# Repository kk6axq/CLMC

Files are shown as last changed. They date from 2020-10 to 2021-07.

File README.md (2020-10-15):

# CLMC (Closed Loop Motor Controller)
This is a closed loop brushed DC motor controller project, completed for an honors enrichment contract in EGR101 at Arizona State University. The goal was to develop the hardware and software to enabled PID based control of position, velocity, and acceleration in an encoder equipped motor. So far, the project has met its minimum requirements, however there are several areas to improve. For more background on the project and architectures, see the Wiki.

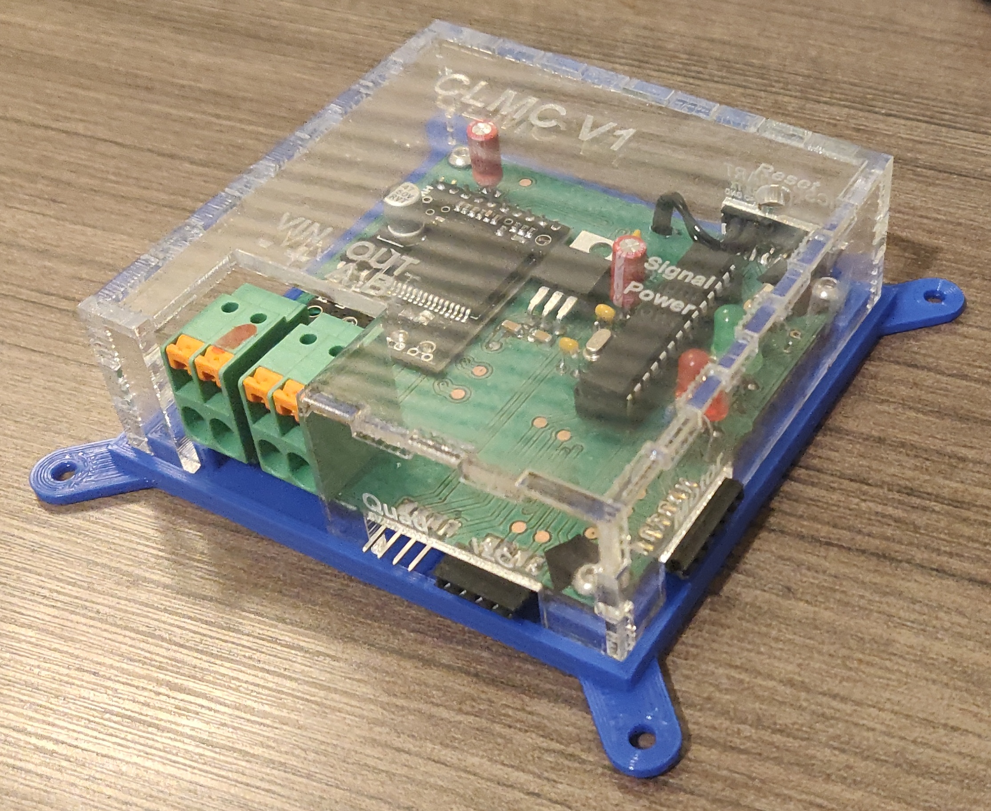
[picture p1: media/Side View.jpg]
Board Photo


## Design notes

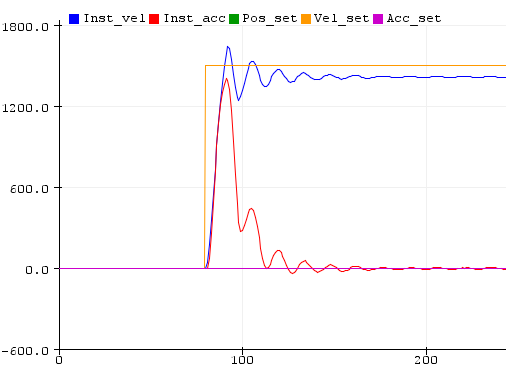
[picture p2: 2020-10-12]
media/Constant Vel Graph - Without Pos.PNG

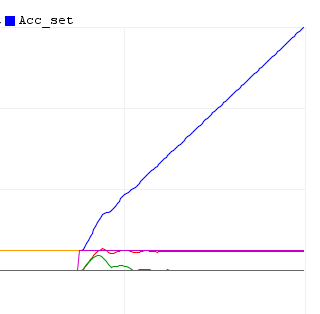
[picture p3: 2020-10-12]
media/Constant Vel Graph - With Pos.PNG

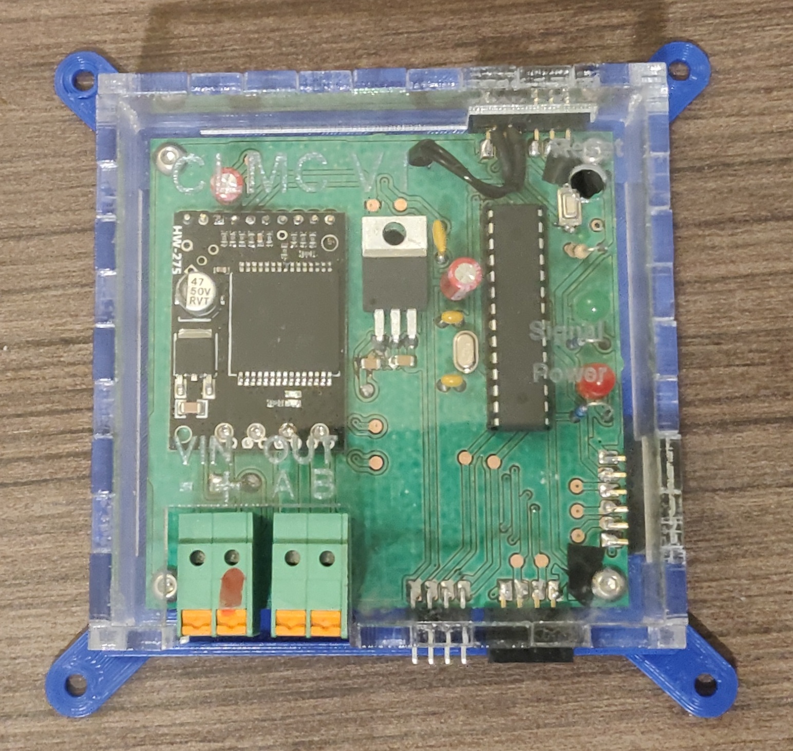
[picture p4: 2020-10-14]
media/Top View.jpg

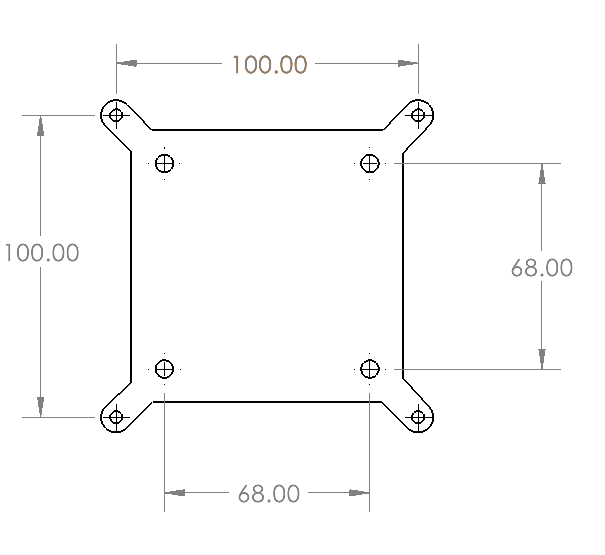
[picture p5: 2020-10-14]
media/Hole Pattern.PNG

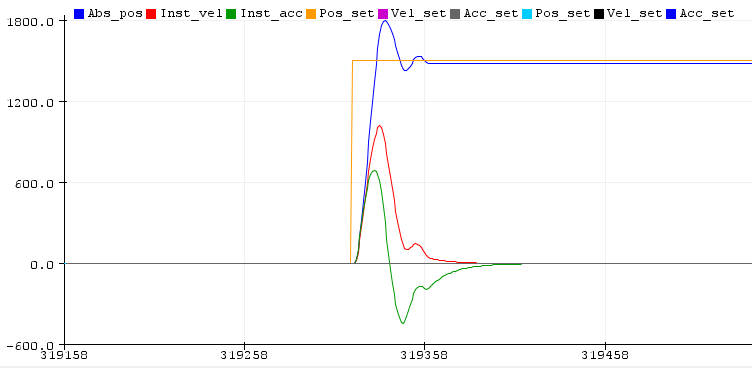
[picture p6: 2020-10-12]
media/Constant Pos Graph.PNG

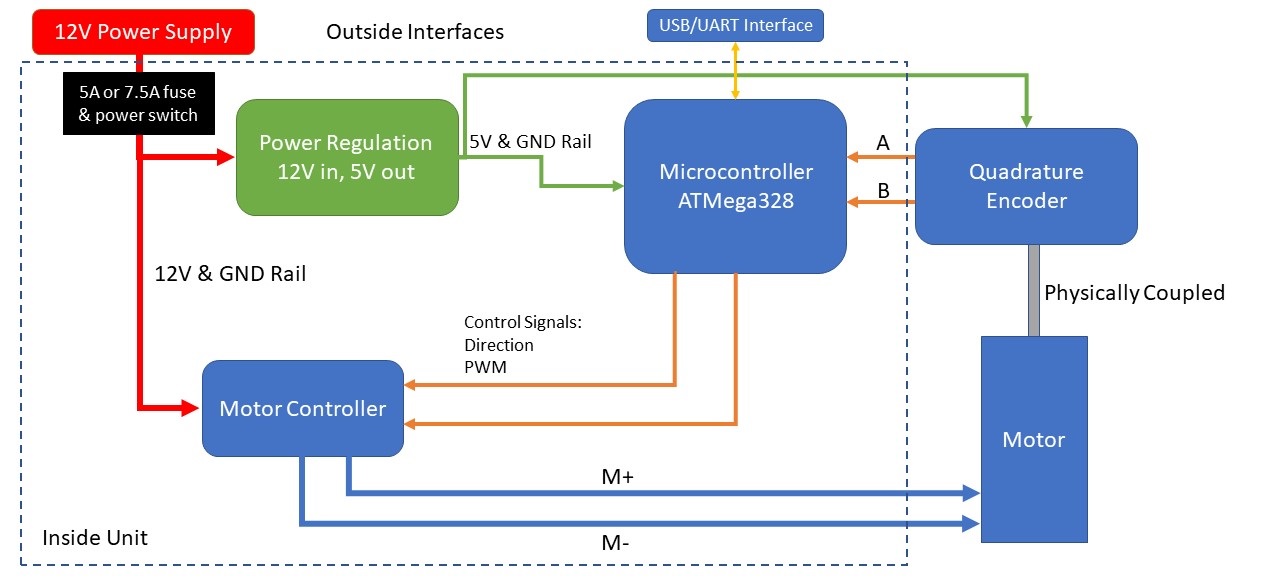
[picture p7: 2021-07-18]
media/Block Diagram.jpg

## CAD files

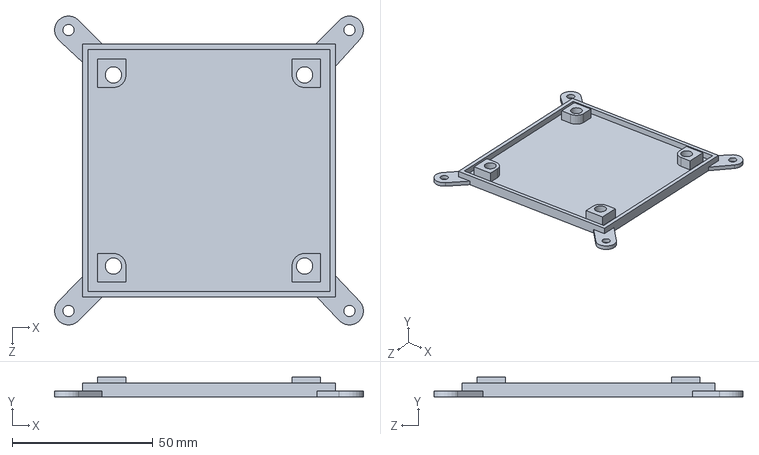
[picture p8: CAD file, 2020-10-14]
hardware/CAD/Main Board Enclosure/PCB Enclosure V1.SLDPRT
109.9 x 7.00 x 109.9 mm

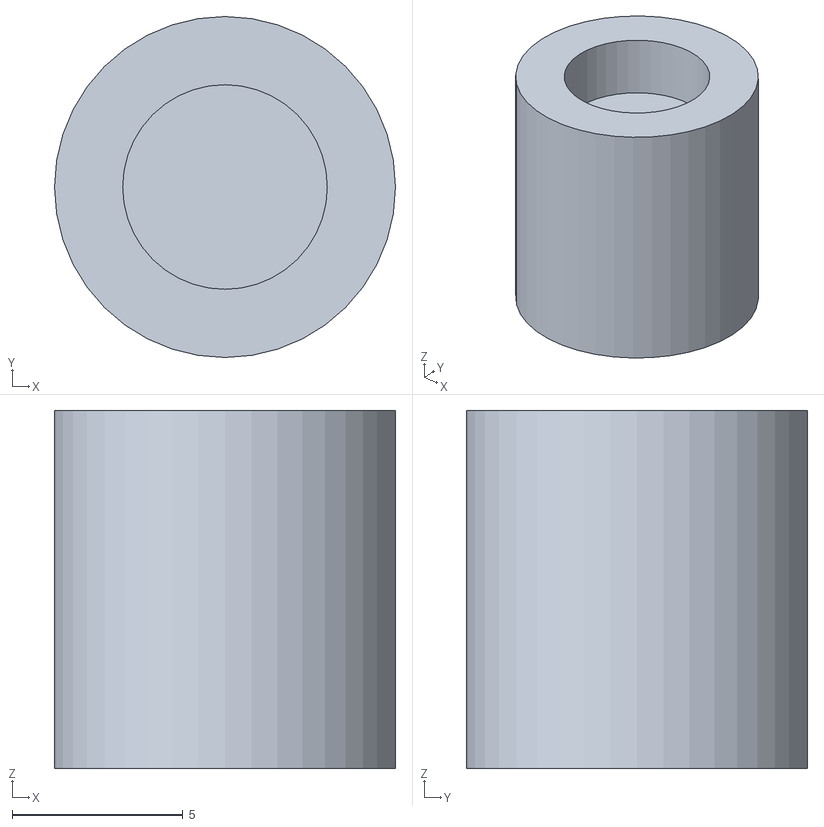
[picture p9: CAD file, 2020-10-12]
hardware/CAD/Motor Magnet Mount/Motor Magnet Mount.stl
10.0 x 10.0 x 10.5

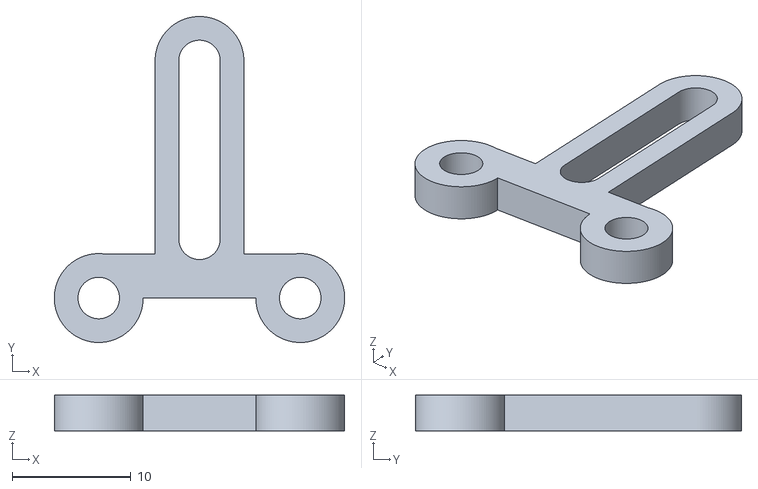
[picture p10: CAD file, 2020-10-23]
hardware/CAD/Sensor Motor Mount/Upper Piece V1.stl
24.5 x 27.5 x 3.00

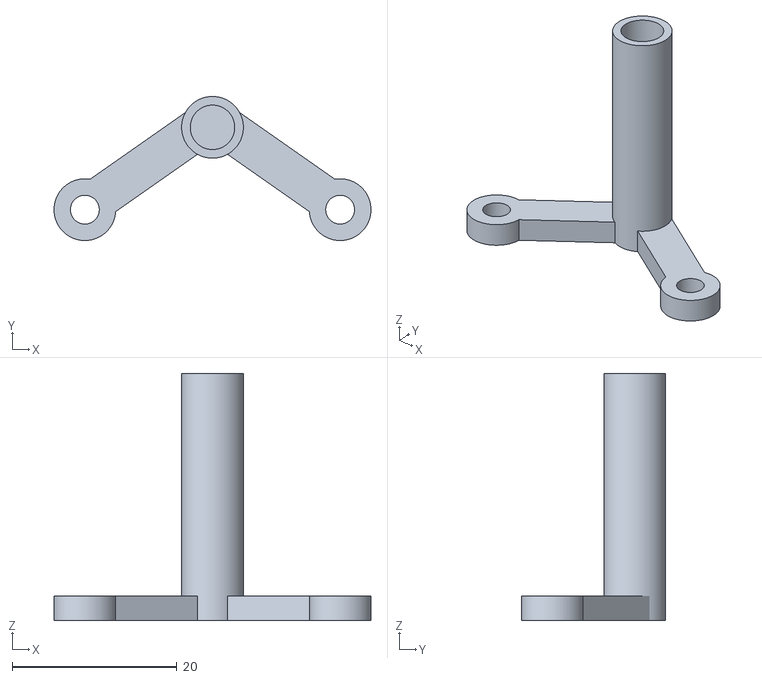
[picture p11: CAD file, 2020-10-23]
hardware/CAD/Sensor Motor Mount/Base Piece V2.stl
38.5 x 17.5 x 30.0

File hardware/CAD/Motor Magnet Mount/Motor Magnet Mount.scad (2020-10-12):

/*
Parametric Magnet Holder
Lukas Severinghaus
September 12, 2020
This program generates a 3d model to hold a magnet of a certain size
on top of a keyed axle. All the dimensions can be changed in the 
variables below.
This program is measurement unit independent.
*/

//Height of the motor axle
axle_height = 6;
//Radius of the motor axle
axle_radius = 3.35; //3.1 was too small
//Distance from the center of the axle to where the key starts
key_offset = 2.4;


//Height of the layer between the motor axle and magnet
separator_height = 2;

//Magnet dimensions
magnet_height = 2.5;
magnet_radius = 3.5; //3.2 was too small

//Wall thickness of the piece
wall_thickness = 2;

//Advanced config parameters
//How many lines to break the circle into
circle_resolution = 80;

//How much extra to cut through the faces, smaller is better
cut_offset = 0.1;

//Radius of the outer containing cylinder.
outer_radius = max(magnet_radius, axle_radius) + wall_thickness;

total_height = axle_height + separator_height + magnet_height;
//Cut the magnet hole
difference(){
    //Cut the axle keyed hole out of the bottom of the piece
    difference() {
        //Define the base cylinder
        cylinder(total_height, outer_radius, outer_radius, $fn=circle_resolution);
        //Move the cylinder down a little to fully cut through the face
        translate([0, 0, -1 * cut_offset]){
            //Cut the key in the shaft
            difference() {
                //Define the shaft cylinder
                cylinder(axle_height + cut_offset, axle_radius, axle_radius, $fn=40);
                //Translate and define the key rectangle
                translate([key_offset, -1 * axle_radius, 0]) {
                    cube([axle_radius - key_offset + cut_offset, axle_radius * 2, axle_height + cut_offset]);
                }
            }
        }
    }

    translate([0, 0, axle_height + separator_height]) {
        cylinder(magnet_height + cut_offset, magnet_radius, magnet_radius, $fn=circle_resolution);
    }
    
    translate([4.5, -10, -1 * cut_offset]) cube([1,25, 20]);
}

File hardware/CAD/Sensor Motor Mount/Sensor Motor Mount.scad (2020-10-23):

/*
Two Piece Motor Mount
Lukas Severinghaus
October 22, 2020
Generates a motor mount to hold the sensor PCB. 
Sized to fit a Pololu 37mm diameter gear motor.
*/

//Set to 1 to view entire assembly
//Set to 2 to view only the base
//Set to 3 to view only the top
view = 1;


hole_size=3.5;
base_hole_spacing = 31;
cr = 100;

post_s = 2;
post_h = 30;

base_h = 3;

top_spacing = 17;

module base(){
difference(){
    union(){
        //Tower
        translate([0, 10, 0]) cylinder(post_h, r1=hole_size/2+2, r2=hole_size/2+2, $fn=cr);
        //Holes

        //Base pieces
        translate([0, 8, 0]) rotate([0, 0, -35]) cube([15, base_h+2, base_h]);
        translate([0, 8, 0]) rotate([0, 0, 180+35]) translate([0, -base_h-2, 0]) cube([15, base_h+2, base_h]);
        translate([-1 * (base_hole_spacing / 2), 0, 0]) cylinder(base_h, r1=hole_size/2+2, r2=hole_size/2+2, $fn=cr);

        translate([(base_hole_spacing / 2), 0, 0]) cylinder(base_h, r1=hole_size/2+2, r2=hole_size/2+2, $fn=cr);
            }

        translate([-1 * (base_hole_spacing / 2), 0, -0.1]) cylinder(5, r1=hole_size/2, r2=hole_size/2, $fn=cr);

        translate([(base_hole_spacing / 2), 0, -0.1]) cylinder(5, r1=hole_size/2, r2=hole_size/2, $fn=cr);
        translate([0, 10, base_h]) cylinder(30, r1=2.7, r2=2.7, $fn=cr);
    }
}
//base();
module upper(){
    difference(){
    union(){
    translate([top_spacing / 2 * -1, 0, 0]) cylinder(base_h, r1=hole_size/2+2, r2=hole_size/2+2, $fn=cr);
    translate([top_spacing / 2, 0, 0]) cylinder(base_h, r1=hole_size/2+2, r2=hole_size/2+2, $fn=cr);
    translate([-9, 0, 0]) cube([18, 3.7, base_h]);
    translate([-1 * (hole_size/2+2), 0, 0]) cube([hole_size+4, 20, base_h]);
    translate([0, 20, 0]) cylinder(base_h, r1=hole_size/2+2, r2=hole_size/2+2, $fn=cr);
    }
    translate([top_spacing / 2 * -1, 0, -0.1]) cylinder(base_h+2, r1=hole_size/2, r2=hole_size/2, $fn=cr);
    translate([top_spacing / 2, 0, -0.1]) cylinder(base_h+2, r1=hole_size/2, r2=hole_size/2, $fn=cr);
    translate([0, 20, -0.1]) cylinder(base_h+0.2, r1=hole_size/2, r2=hole_size/2, $fn=cr);
    translate([0, 5, -0.1]) cylinder(base_h+0.2, r1=hole_size/2, r2=hole_size/2, $fn=cr);
    translate([-1 * (hole_size / 2), 5, -0.1]) cube([hole_size, 15, base_h + 0.2]);
}
}
if(view==1){
    base();
    translate([0, -10, 30]) upper();
}else if(view == 2){
    base();
}else if(view == 3){
    upper();
}    

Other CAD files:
hardware/CAD/Main Board Enclosure/PCB Enclosure V1.STL

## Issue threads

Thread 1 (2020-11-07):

Current spikes on motor cold start

kk6axq, 2020-11-07:
When driving a Tetrix motor, there's an initial current spike when transitioning from a low output to full output (255 or -255), causing the microcontroller to reset when running on bench power.

Information:
The current sensor read a maximum of 2.06, however my bench power supply briefly triggered an over current warning at 6 amps. The signal LED flashed the startup sequence immediately after this and the previous command was not retained, so the microcontroller definitely reset.

Steps to reproduce:
* Connect to bench supply.
* Send the command `r1500`.
* Microcontroller resets.
Issue:
This probably stems from a brownout in the 5V rail, stemming from either the current protection reducing the voltage or the high current draw reducing the voltage. This suggests that there is a very brief high current spike when starting the motor to full speed.

The motor's internal resistance is 5-6 Ohms, which should draw 2A given V=IR, so that further supports the startup spike theory.

Possible solutions:
* Run it on battery power or a higher current supply. When powering it from a NiMH battery, the microcontroller does not reset.
* Add a capacitor to the 12V rail. This would maybe help keep the rail within the 5V regulator's usable range, though it might have to be a big capacitor.
* Add a capacitor to the 5V rail. This would buffer the 5V rail while the voltage drops, though I don't know what effect this would have on the motor driver.

kk6axq, 2020-11-18:
This is just inherent to the design. An additional capacitor could be added, but that distracts from the larger issue of not having a suitable power source. I'll close this for now and it can be reopened if it becomes an issue down the road.

Closed 2020-11-18.

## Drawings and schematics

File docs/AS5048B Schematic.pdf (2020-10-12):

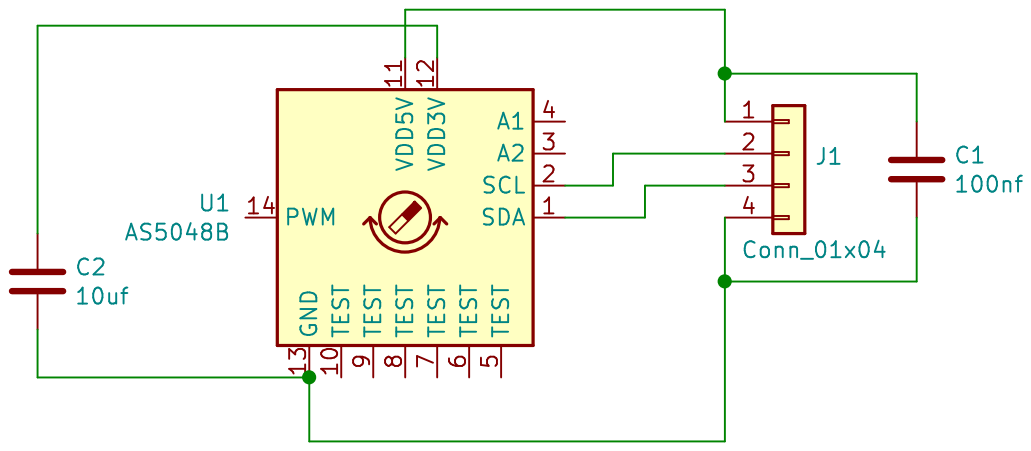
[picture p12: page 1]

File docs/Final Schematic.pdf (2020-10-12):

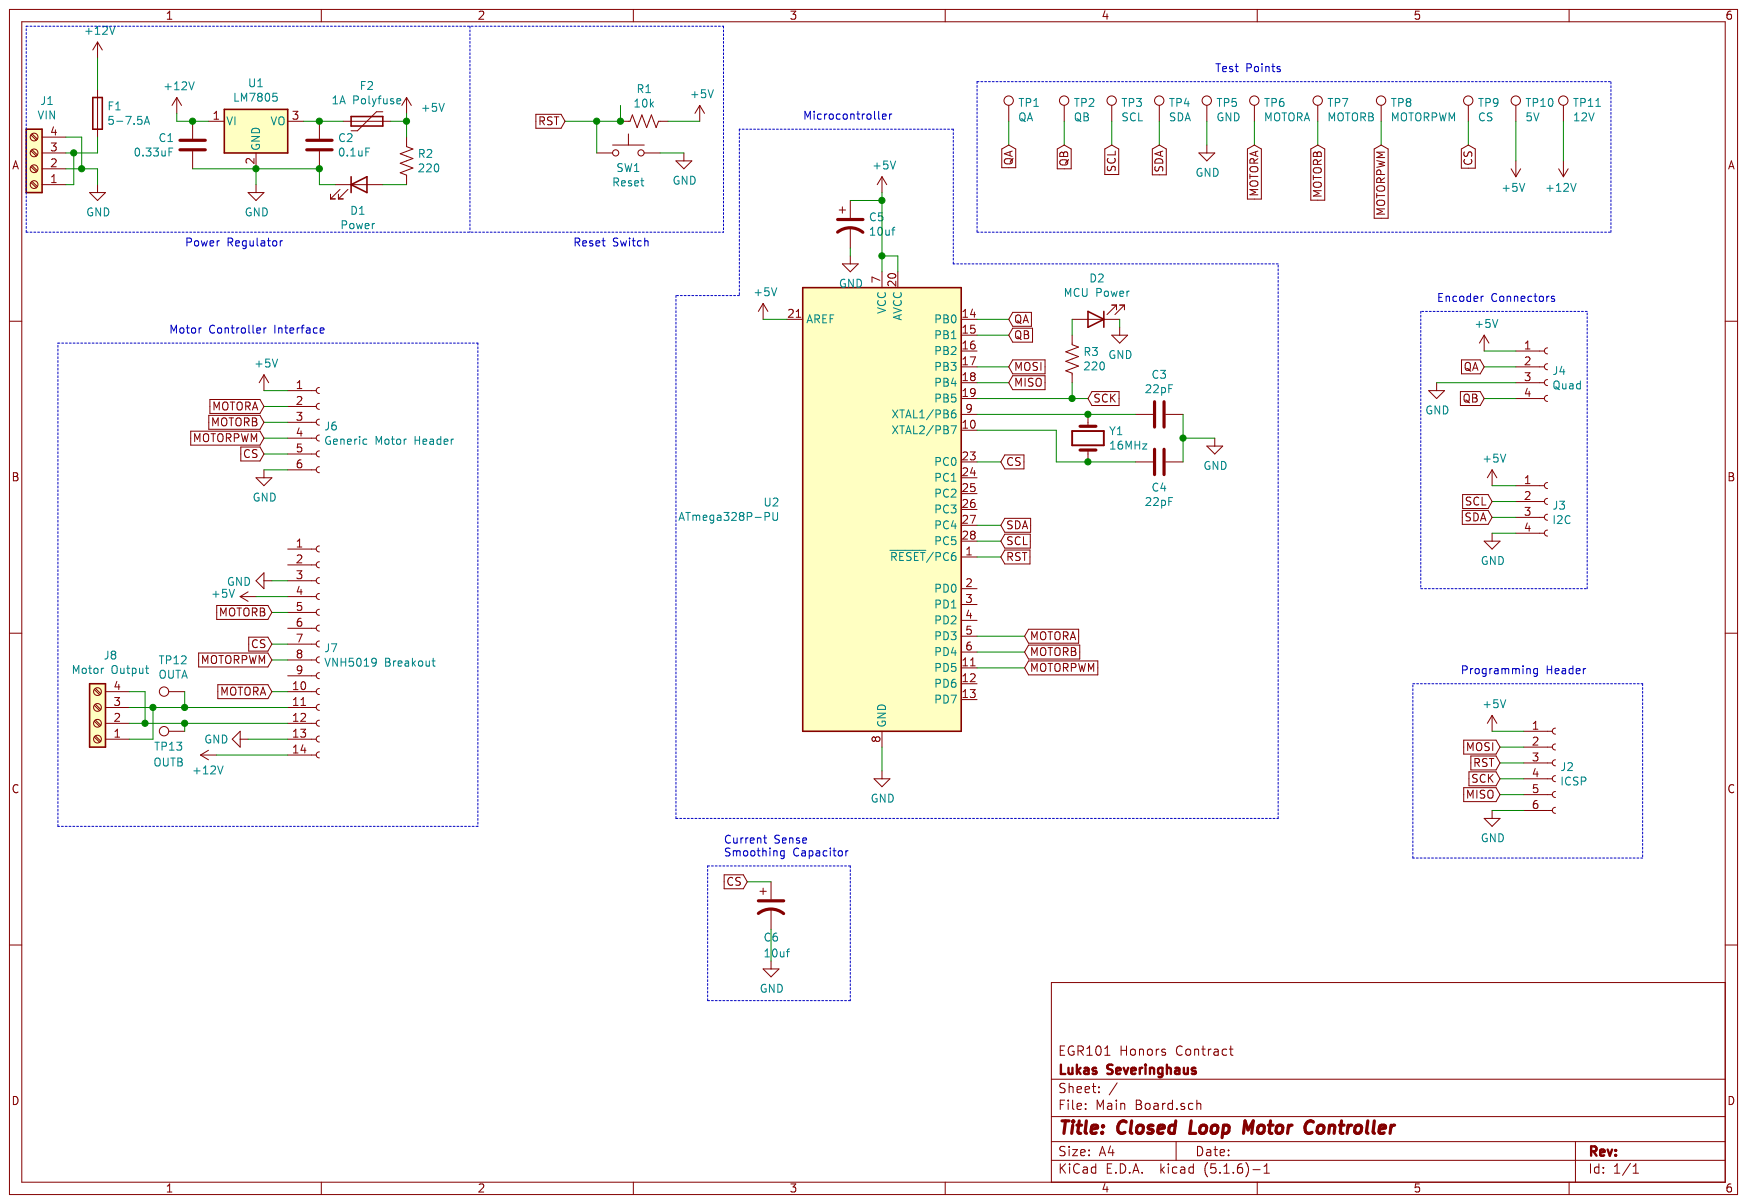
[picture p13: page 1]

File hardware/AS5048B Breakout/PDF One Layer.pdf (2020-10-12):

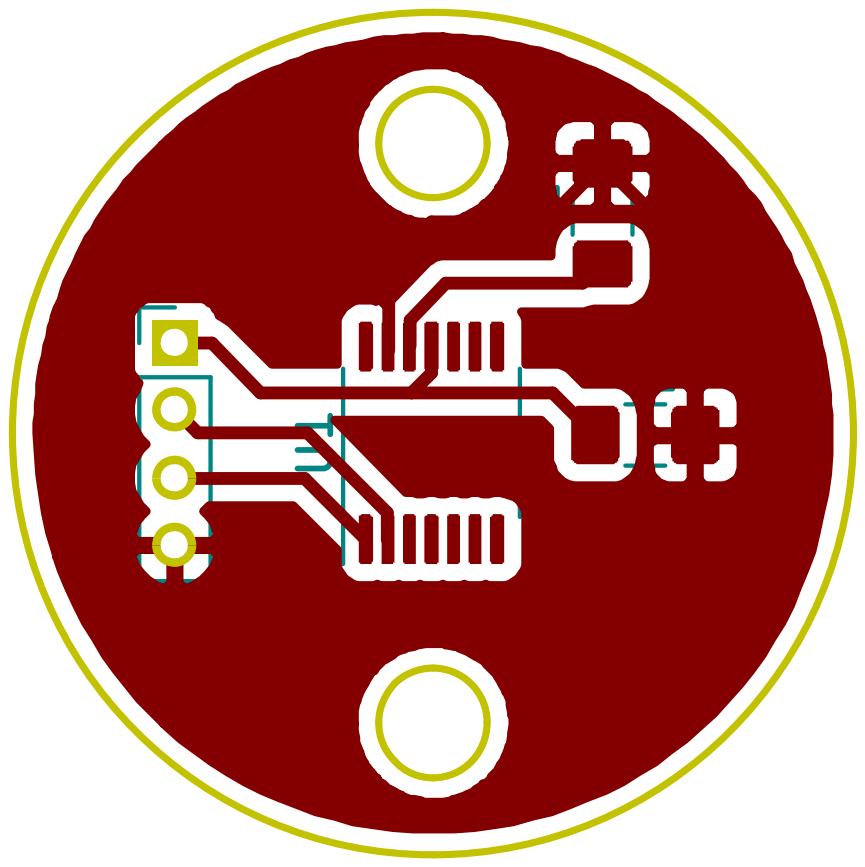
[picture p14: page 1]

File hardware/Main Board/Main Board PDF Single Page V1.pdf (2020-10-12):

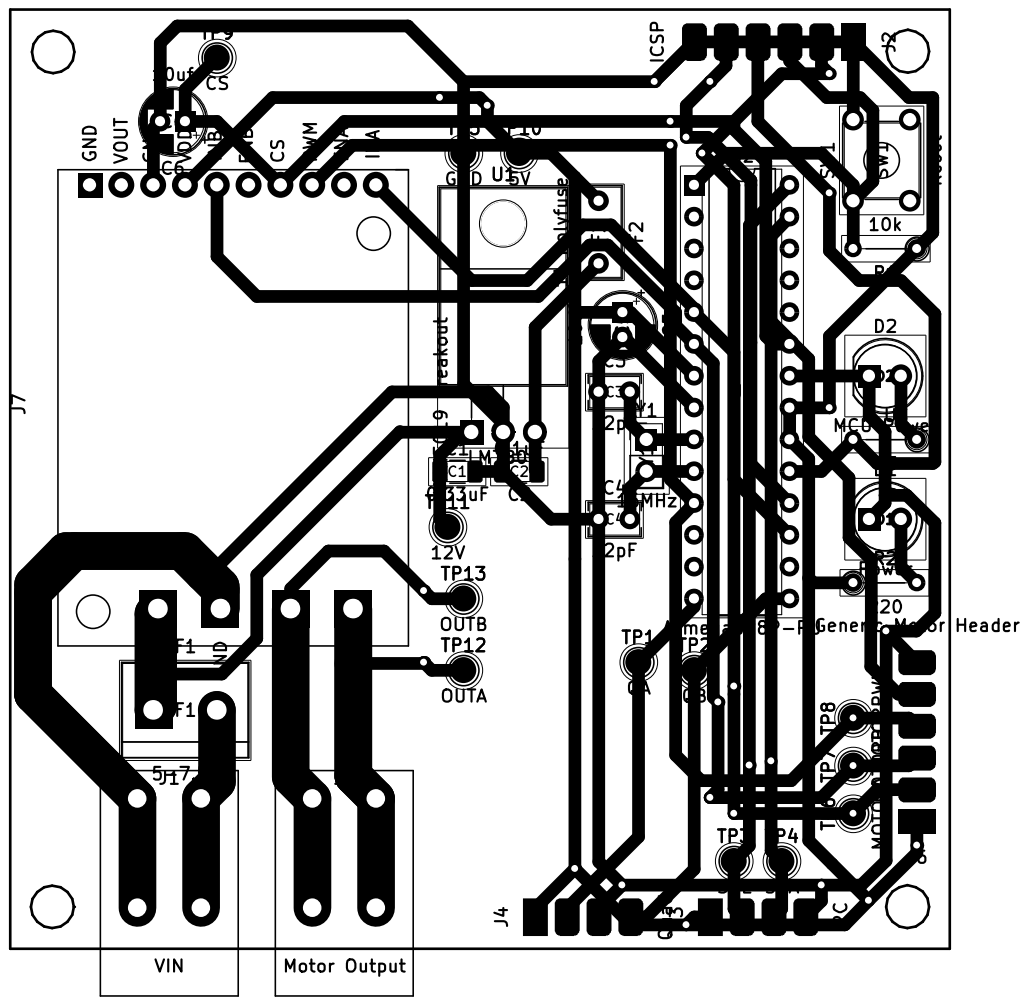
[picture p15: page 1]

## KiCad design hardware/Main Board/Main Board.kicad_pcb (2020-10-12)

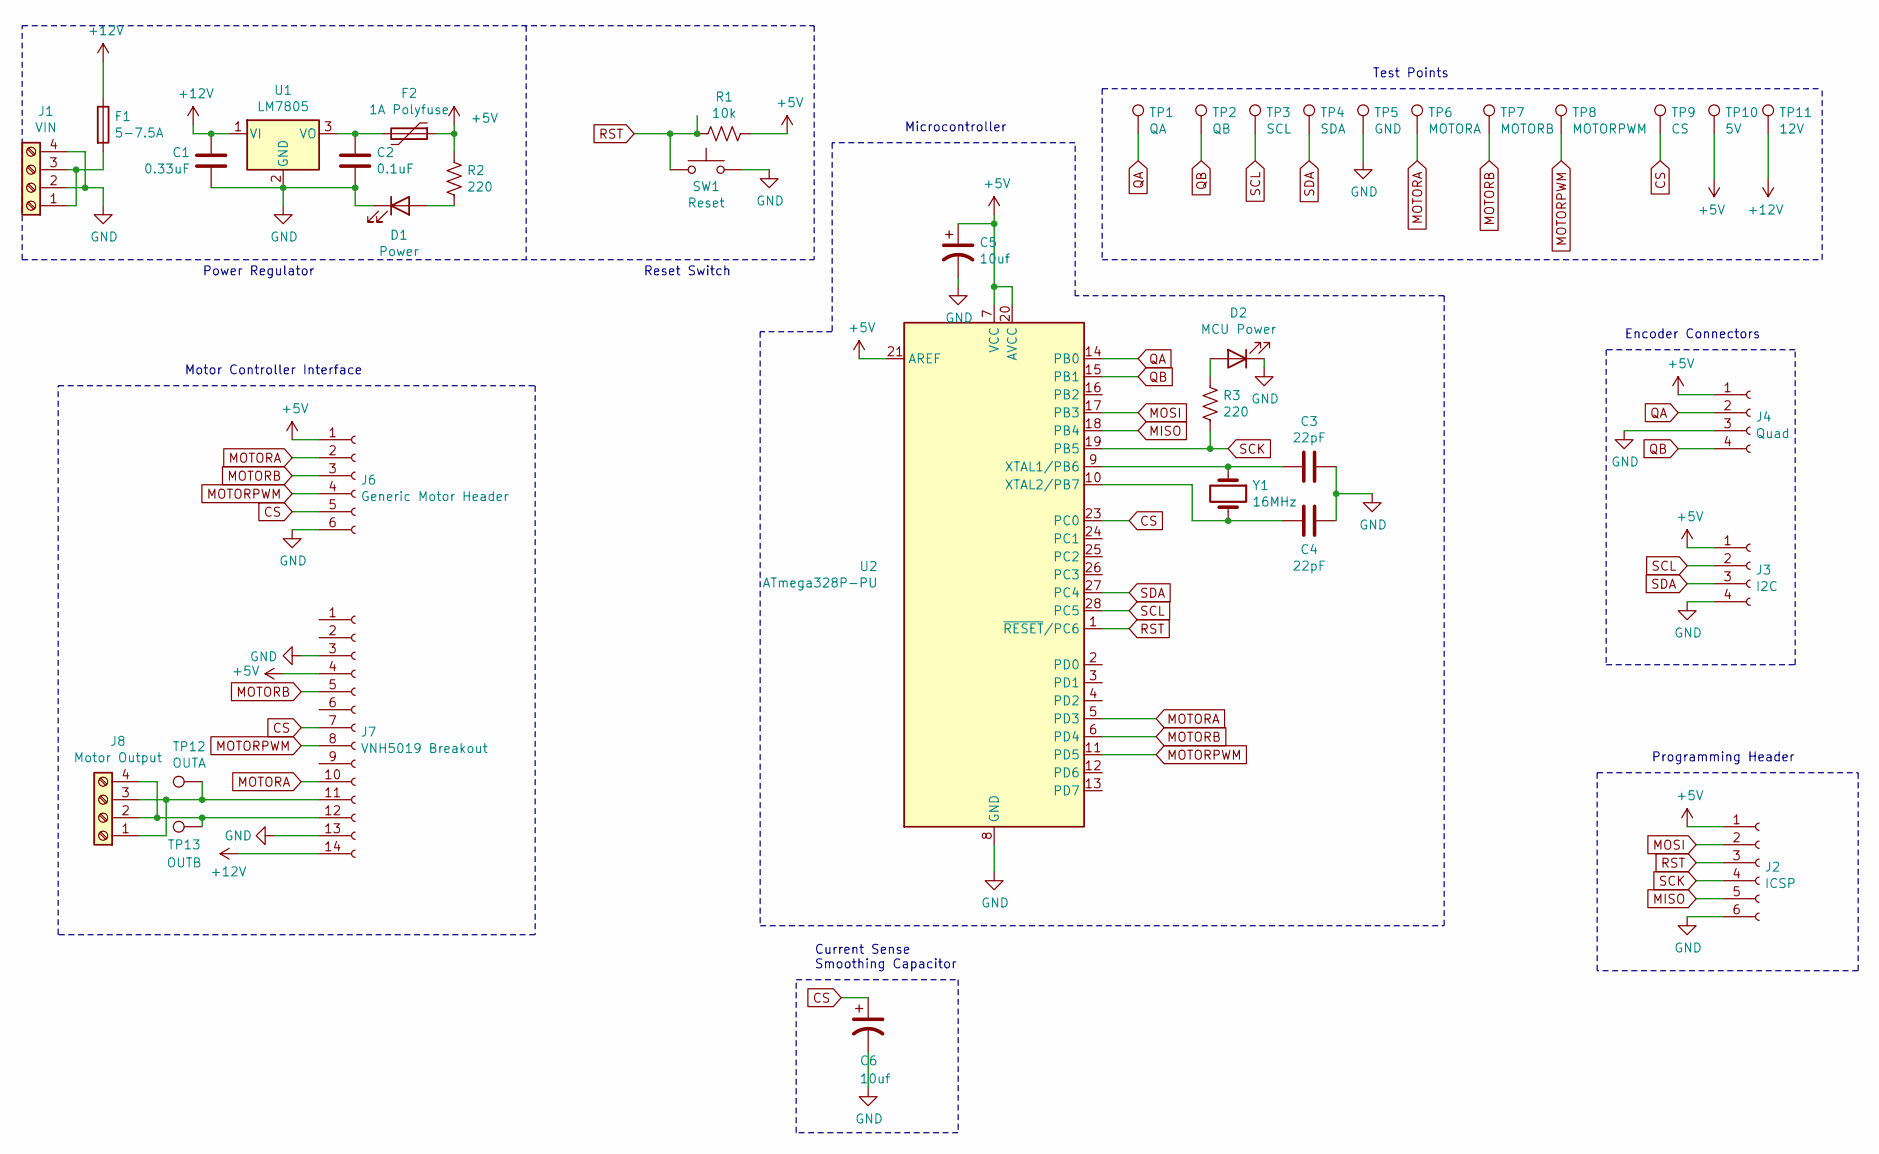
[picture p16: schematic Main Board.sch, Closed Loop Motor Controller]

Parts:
C1: 0.33uF; C_1206_3216Metric
C2: 0.1uF; C_1206_3216Metric
C3, C4: 22pF; C_Rect_L4.0mm_W2.5mm_P2.50mm
C5, C6: 10uf; CP_Radial_D5.0mm_P2.00mm
D1: Power; LED_D5.0mm
D2: MCU Power; LED_D5.0mm
F1: 5-7.5A; TerminalBlock_bornier-2_P5.08mm
F2: 1A Polyfuse; C_Rect_L7.2mm_W3.5mm_P5.00mm_FKS2_FKP2_MKS2_MKP2
J1: VIN; 2x2TerminalBlock
J2: ICSP; 6PinEdgeConnector
J3: I2C; 4PinEdgeConnector
J4: Quad; 4PinEdgeConnector
J6: Generic Motor Header; 6PinEdgeConnector
J7: VNH5019 Breakout; VNH5019Footprint
J8: Motor Output; 2x2TerminalBlock
R1: 10k; R_Axial_DIN0204_L3.6mm_D1.6mm_P5.08mm_Vertical
R2, R3: 220; R_Axial_DIN0204_L3.6mm_D1.6mm_P5.08mm_Vertical
SW1: Reset; SW_TH_Tactile_Omron_B3F-10xx
TP1: QA; TestPoint_Pad_D2.0mm
TP2: QB; TestPoint_Pad_D2.0mm
TP3: SCL; TestPoint_Pad_D2.0mm
TP4: SDA; TestPoint_Pad_D2.0mm
TP5: GND; TestPoint_Pad_D2.0mm
TP6: MOTORA; TestPoint_Pad_D2.0mm
TP7: MOTORB; TestPoint_Pad_D2.0mm
TP8: MOTORPWM; TestPoint_Pad_D2.0mm
TP9: CS; TestPoint_Pad_D2.0mm
TP10: 5V; TestPoint_Pad_D2.0mm
TP11: 12V; TestPoint_Pad_D2.0mm
TP12: OUTA; TestPoint_Pad_D2.0mm
TP13: OUTB; TestPoint_Pad_D2.0mm
U1: LM7805; TO-220-3_Horizontal_TabDown
U2: ATmega328P-PU; DIP-28_W7.62mm
Y1: 16MHz; PinHeader_1x02_P2.54mm_Vertical

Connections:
+5V: C5.1, F2.1, J2.1, J3.1, J4.1, J6.1, J7.4, R1.1, R2.1, TP10.1, U2.7 (VCC), U2.20 (AVCC), U2.21 (AREF)
+12V: C1.1, F1.1, J7.14, TP11.1, U1.1 (VI)
CS: C6.1, J6.5, J7.7, TP9.1, U2.23 (PC0)
GND: C1.2, C2.2, C3.1, C4.1, C5.2, C6.2, D1.1 (K), D2.1 (K), J1.2, J1.4, J2.6, J3.4, J4.3, J6.6, J7.3, J7.13, SW1.2, TP5.1, U1.2 (GND), U2.8 (GND), U2.22 (GND)
MISO: J2.5, U2.18 (PB4)
MOSI: J2.2, U2.17 (PB3)
MOTORA: J6.2, J7.10, TP6.1, U2.5 (PD3)
MOTORB: J6.3, J7.5, TP7.1, U2.6 (PD4)
MOTORPWM: J6.4, J7.8, TP8.1, U2.11 (PD5)
unnamed: C2.1, F2.2, U1.3 (VO)
unnamed: C3.2, U2.9 (XTAL1/PB6), Y1.1
unnamed: C4.2, U2.10 (XTAL2/PB7), Y1.2
unnamed: D1.2 (A), R2.2
unnamed: D2.2 (A), R3.1
unnamed: F1.2, J1.1, J1.3
unnamed: J7.11, J8.1, J8.3, TP12.1
unnamed: J7.12, J8.2, J8.4, TP13.1
QA: J4.2, TP1.1, U2.14 (PB0)
QB: J4.4, TP2.1, U2.15 (PB1)
RST: J2.3, R1.2, SW1.1, U2.1 (~RESET~/PC6)
SCK: J2.4, R3.2, U2.19 (PB5)
SCL: J3.2, TP3.1, U2.28 (PC5)
SDA: J3.3, TP4.1, U2.27 (PC4)

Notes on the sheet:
Power Regulator
Test Points
Programming Header
Encoder Connectors
Microcontroller
Reset Switch
Current Sense Smoothing Capacitor
Motor Controller Interface

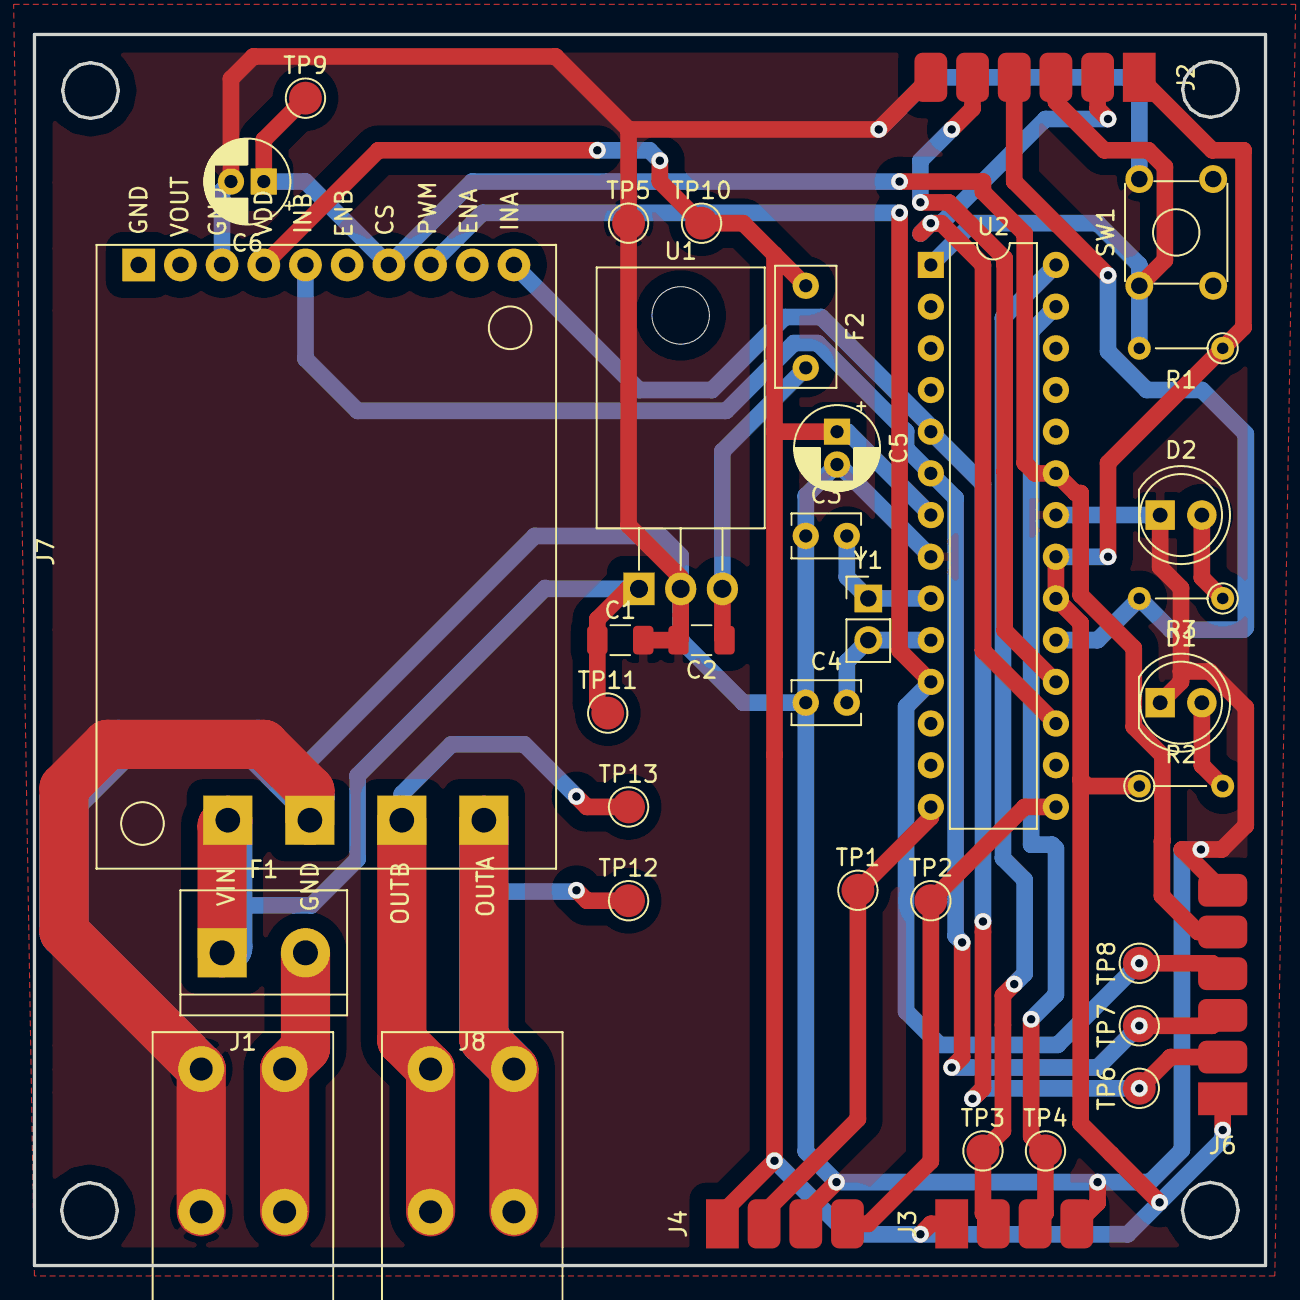
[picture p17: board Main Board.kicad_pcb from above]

Board: 2 copper layers, 75.0 x 75.0 mm, 37 parts (0 on the bottom side), 23 nets.

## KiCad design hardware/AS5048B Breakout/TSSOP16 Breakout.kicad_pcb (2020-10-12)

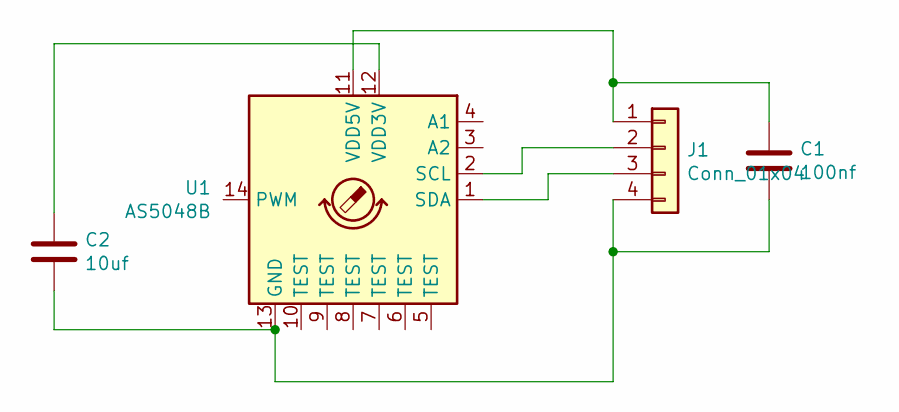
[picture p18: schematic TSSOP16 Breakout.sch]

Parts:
C1: 100nf; C_1206_3216Metric_Pad1.42x1.75mm_HandSolder
C2: 10uf; C_1206_3216Metric_Pad1.42x1.75mm_HandSolder
J1: Conn_01x04; PinHeader_1x04_P2.00mm_Vertical
U1: AS5048B; TSSOP-14_4.4x5mm_P0.65mm

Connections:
unnamed: C1.1, J1.1, U1.11 (VDD5V)
unnamed: C1.2, C2.2, J1.4, U1.13 (GND)
unnamed: C2.1, U1.12 (VDD3V)
unnamed: J1.2, U1.2 (SCL)
unnamed: J1.3, U1.1 (SDA)

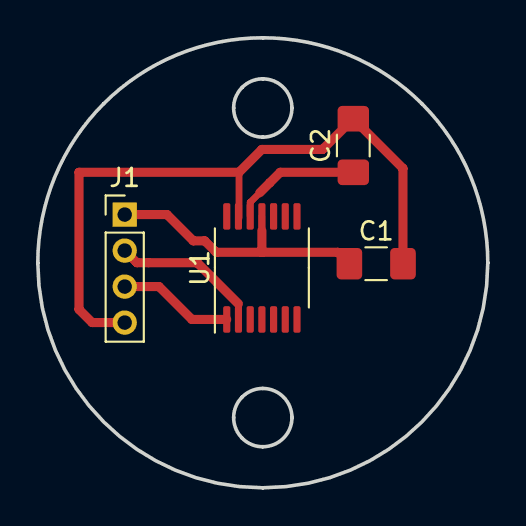
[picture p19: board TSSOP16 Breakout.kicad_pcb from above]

Board: 2 copper layers, 25.0 x 25.0 mm, 4 parts (0 on the bottom side), 5 nets.

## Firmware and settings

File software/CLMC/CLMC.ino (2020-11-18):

/**
   File: CLMC.ino
   Author: Lukas Severinghaus
   Date: October 11, 2020
   Purpose: Control code for ATMega328p based PID motor controller.
   Completed as part of an honors enrichment contract for EGR101 at ASU.

   License:
   Copyright (C) 2020  Lukas Severinghaus

   This program is free software; you can redistribute it and/or
   modify it under the terms of the GNU General Public License version 3
   as published by the Free Software Foundation;

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
   You should have received a copy of the GNU General Public License
   along with this program; if not, write to the Free Software
   Foundation, Inc., 51 Franklin Street, Fifth Floor, Boston, MA  02110-1301, USA.
*/
//Uncomment to load config and PIDs from EEPROM on boot.
#define LOAD_CONFIG_ON_BOOT

//Serial baud rate
#define BAUD_RATE 9600

//Pin that signalling LED is connected to
#define LED_PIN 13



#define TUNE_NONE 0
#define TUNE_POS 1
#define TUNE_VEL 2
#define TUNE_ACC 3
void setup() {

  Serial.begin(BAUD_RATE);

  init_motor();
  init_encoders();
  init_pid();

  pinMode(LED_PIN, OUTPUT);
  for (int i = 0; i < 3; i++) {
    digitalWrite(LED_PIN, HIGH);
    delay(100);
    digitalWrite(LED_PIN, LOW);
    delay(100);
  }
#ifdef LOAD_CONFIG_ON_BOOT
  load_config();
#endif
}

//Flag for enabling motor output.
bool control = true;

void loop() {
  //Read from Serial, if bytes are available
  if (Serial.available() > 0) {
    char s = Serial.read();
    //Check if the character matches a command letter
    if (s == 'r') {
      constant_pos(Serial.parseInt());
    } else if (s == 'f') {
      constant_vel(Serial.parseInt());
    } else if (s == 'v') {
      constant_acc(Serial.parseFloat());
    } else if (s == 'e') {
      control = true;
    } else if (s == 'w') {
      control = false;
      command_motor(0);
    } else if (s == 'p') {
      tune_p(Serial.parseFloat());
    } else if (s == 'i') {
      tune_i(Serial.parseFloat());
    } else if (s == 'd') {
      tune_d(Serial.parseFloat());
    } else if (s == 's') {
      if (get_tune_mode() == TUNE_POS || get_tune_mode() == TUNE_VEL) {
        command_tune(Serial.parseInt());
      } else if (get_tune_mode() == TUNE_ACC) {
        command_tune(Serial.parseFloat());
      } else {
        Serial.println("No tuning mode currently set.");
      }
    } else if (s == 't') { //Set controller to tune.
      serial_wait_timeout(1, 20);
      char a = Serial.read();
      Serial.println(a);
      if (a == 'p') {
        Serial.println("Selecting position controller");
        set_tune_mode(TUNE_POS);
      } else if (a == 'v') {
        Serial.println("Selecting velocity controller");
        set_tune_mode(TUNE_VEL);
      } else if (a == 'a') {
        Serial.println("Selecting acceleration controller");
        set_tune_mode(TUNE_ACC);
      } else {
        Serial.println("Deselecting tuned controller");
        set_tune_mode(TUNE_NONE);
      }
    } else if (s == 'j') {
      set_inst_vel_filter(Serial.parseFloat());
    } else if (s == 'l') {
      Serial.println("Loading config from EEPROM");
      load_config();
    } else if (s == 'k') {
      Serial.println("Saving config to EEPROM");
      save_config();
    } else if (s == 'z') {
      print_pids();
    } else if (s == 'x') {
      print_EEPROM();
    } else if (s == 'h') {
      Serial.println("\n**** Commands ****");
      Serial.println("r<int>\tConstant Position");
      Serial.println("f<int>\tConstant Velocity");
      Serial.println("v<float>\tConstant Acceleration");
      Serial.println("e\tEnable Output");
      Serial.println("w<int>\tDisable Output");
      Serial.println("t[p,v,a]\tSelect controller to tune");
      Serial.println("p<float>\tSet P component of tuned controller");
      Serial.println("i<float>\tSet I component of tuned controller");
      Serial.println("d<float>\tSet D component of tuned controller");
      Serial.println("j<float>\tSet strength of velocity particle filter");
      Serial.println("z\tPrint PID values");
      Serial.println("x\tPrint EEPROM values");
      Serial.println("k\tSave configuration to EEPROM");
      Serial.println("l\tLoad configuration from EEPROM");
      Serial.println("h\tShow help menu");
    }
  }


  //Diagnostic output:
  //Measured outputs, position, velocity, and acceleration
  Serial.print("Inst_vel: ");
  Serial.print(get_inst_velocity());
  Serial.print("\tInst_acc: ");
  Serial.print(get_inst_acceleration());

  if (get_tune_mode() == TUNE_POS) {
    Serial.print("\tAbs_pos: ");
    Serial.print(get_raw_count());
  }
  //Setpoints
  Serial.print("\tPos_set: ");
  Serial.print(get_pos_setpoint());
  Serial.print("\tVel_set: ");
  Serial.print(get_vel_setpoint());
  Serial.print("\tAcc_set: ");
  Serial.print(get_acc_setpoint());
  Serial.print("\tOutput: ");
  Serial.print(get_pid_output());
  Serial.print("\tCurrent: ");
  Serial.print(get_current());
  Serial.println();

  update_pid();
  if (control) command_motor(get_pid_output());

}
/**
 * Waits for serial bytes, or timeout, whichever comes first.
 * len: number of bytes to wait for.
 * timeout: timeout in ms to wait for bytes.
 * Returns nothing.
 */
void serial_wait_timeout(int len, int timeout){
  long start_t = millis();
  while(Serial.available() < len && millis() < timeout + start_t);
  Serial.print("Waited: "); Serial.println(millis() - start_t);
}
bool get_control() {
  return control;
}

void set_control(bool val) {
  control = val;
}

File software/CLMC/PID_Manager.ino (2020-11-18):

/**
   File: PID_Manager.ino
   Author: Lukas Severinghaus
   Date: October 11, 2020
   Purpose: Interfaces with PID control library.

   License:
   Copyright (C) 2020  Lukas Severinghaus

   This program is free software; you can redistribute it and/or
   modify it under the terms of the GNU General Public License version 3
   as published by the Free Software Foundation;

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
   You should have received a copy of the GNU General Public License
   along with this program; if not, write to the Free Software
   Foundation, Inc., 51 Franklin Street, Fifth Floor, Boston, MA  02110-1301, USA.
*/
/**
   Sources referenced during development:
   Filter: https://dsp.stackexchange.com/questions/41854/low-pass-filter-algorithm-origin
*/

#define TUNE_ERROR "Not currently in tuning mode."
byte tune_mode = TUNE_NONE;

//Constant velocity error is change in position for right now + error from last period
#define CONSTANT_ACC 0
#define CONSTANT_VEL 1
#define CONSTANT_POS 2
#define RAW 3

#include <PIDController.h>

PIDController position_controller;
PIDController velocity_controller;
PIDController acceleration_controller;
int pid_freq = 50;
int pid_period = 1000 / pid_freq;
long last_pid_loop = 0;


float pos_kp = 2;
float pos_ki = 0.2;
float pos_kd = 0;


float vel_kp = 1;
float vel_ki = 0.4;
float vel_kd = 0.3;

float acc_kp = 0.8;
float acc_ki = 0.3;
float acc_kd = 0;

double pos_setpoint = 0;
double vel_setpoint = 0;
double acc_setpoint = 0;

byte current_state = RAW;

void init_pid() {
  position_controller.begin();
  position_controller.setpoint(pos_setpoint);
  position_controller.tune(pos_kp, pos_ki, pos_kd);
  position_controller.limit(-255, 255);

  velocity_controller.begin();
  velocity_controller.setpoint(vel_setpoint);
  velocity_controller.tune(vel_kp, vel_ki, vel_kd);
  velocity_controller.limit(-255, 255);

  acceleration_controller.begin();
  acceleration_controller.setpoint(acc_setpoint);
  acceleration_controller.tune(acc_kp, acc_ki, acc_kd);
  acceleration_controller.limit(-255, 255);
}
void update_pid() {
  if (millis() > last_pid_loop + pid_period) {
    calculate_instantaneous();
    if (current_state == CONSTANT_ACC) {
      acceleration_controller.compute(get_inst_acceleration());
    } else if (current_state == CONSTANT_VEL) {
      velocity_controller.compute(get_inst_velocity());
    } else if (current_state == CONSTANT_POS) {
      position_controller.compute(get_raw_count());
    } else if (current_state == RAW) {
      //Do nothing.
    }
  }
}

int get_pid_output() {
  if (current_state == CONSTANT_ACC) {
    return acceleration_controller.getOutput();
  } else if (current_state == CONSTANT_VEL) {
    return velocity_controller.getOutput();
  } else if (current_state == CONSTANT_POS) {
    return position_controller.getOutput();
  } else {
    return 0; //Fail safe, if in raw mode.
  }
}
void set_state(int st) {
  current_state = st;
}
void constant_pos(long setpoint) {
  set_state(CONSTANT_POS);
  pos_setpoint = setpoint;
  position_controller.setpoint(setpoint);
}

void constant_vel(float vel) {
  set_state(CONSTANT_VEL);
  vel_setpoint = vel;
  velocity_controller.setpoint(vel);
}

void constant_acc(float acc) {
  set_state(CONSTANT_ACC);
  acc_setpoint = acc;
  acceleration_controller.setpoint(acc);
}

/**** Setpoint getters ****/
int get_pos_setpoint() {
  return pos_setpoint;
}

int get_vel_setpoint() {
  return vel_setpoint;
}

int get_acc_setpoint() {
  return acc_setpoint;
}
/**** Position PID modifiers ****/
void pos_p(float p) {
  pos_kp = p;
  update_pos_tune();
}

float pos_p() {
  return pos_kp;
}
void pos_i(float i) {
  pos_ki = i;
  update_pos_tune();
}

float pos_i() {
  return pos_ki;
}

void pos_d(float d) {
  pos_kd = d;
  update_pos_tune();
}

float pos_d() {
  return pos_kd;
}

void update_pos_tune() {
  position_controller.tune(pos_kp, pos_ki, pos_kd);
}
/**** Velocity PID modifiers ****/
void vel_p(float p) {
  vel_kp = p;
  update_vel_tune();
}

float vel_p() {
  return vel_kp;
}

void vel_i(float i) {
  vel_ki = i;
  update_vel_tune();
}

float vel_i() {
  return vel_ki;
}

void vel_d(float d) {
  vel_kd = d;
  update_vel_tune();
}

float vel_d() {
  return vel_kd;
}

void update_vel_tune() {
  velocity_controller.tune(vel_kp, vel_ki, vel_kd);
}
/**** Acceleration PID modifiers ****/
void acc_p(float p) {
  acc_kp = p;
  update_acc_tune();
}

float acc_p() {
  return acc_kp;
}

void acc_i(float i) {
  acc_ki = i;
  update_acc_tune();
}

float acc_i() {
  return acc_ki;
}

void acc_d(float d) {
  acc_kd = d;
  update_acc_tune();
}

float acc_d() {
  return acc_kd;
}

void update_acc_tune() {
  acceleration_controller.tune(acc_kp, acc_ki, acc_kd);
}

void tune_p(float p) {
  if (tune_mode == TUNE_POS) {
    pos_kp = p;
    update_pos_tune();
  } else if (tune_mode == TUNE_VEL) {
    vel_kp = p;
    update_vel_tune();
  } else if (tune_mode == TUNE_ACC) {
    acc_kp = p;
    update_acc_tune();
  }
}

void tune_i(float i) {
  if (tune_mode == TUNE_POS) {
    pos_ki = i;
    update_pos_tune();
  } else if (tune_mode == TUNE_VEL) {
    vel_ki = i;
    update_vel_tune();
  } else if (tune_mode == TUNE_ACC) {
    acc_ki = i;
    update_acc_tune();
  }
}

void tune_d(float d) {
  if (tune_mode == TUNE_POS) {
    pos_kd = d;
    update_pos_tune();
  } else if (tune_mode == TUNE_VEL) {
    vel_kd = d;
    update_vel_tune();
  } else if (tune_mode == TUNE_ACC) {
    acc_kd = d;
    update_acc_tune();
  } else {
    Serial.println(TUNE_ERROR);
  }
}
//Sets the setpoint of the currently active tune.
void command_tune(float val) {
  if (tune_mode == TUNE_POS) {
    constant_pos(val);
  } else if (tune_mode == TUNE_VEL) {
    constant_vel(val);
  } else if (tune_mode == TUNE_ACC) {
    constant_acc(val);
  } else {
    Serial.println(TUNE_ERROR);
  }

}

byte get_PID_current_state() {
  return current_state;
}

void set_PID_current_state(byte state) {
  current_state = state;
}

byte get_tune_mode() {
  return tune_mode;
}

void set_tune_mode(byte b) {
  tune_mode = b;
}

void print_pids(){
  Serial.println("**** PID Values ****");
  Serial.println("Position: ");
  Serial.print("\tP:"); Serial.println(pos_kp);
  Serial.print("\tI:"); Serial.println(pos_ki);  
  Serial.print("\tD:"); Serial.println(pos_kd);
  Serial.println("");
  Serial.println("Velocity: ");
  Serial.print("\tP:"); Serial.println(vel_kp);
  Serial.print("\tI:"); Serial.println(vel_ki);  
  Serial.print("\tD:"); Serial.println(vel_kd);
  Serial.println("");
  Serial.println("Acceleration: ");
  Serial.print("\tP:"); Serial.println(acc_kp);
  Serial.print("\tI:"); Serial.println(acc_ki);  
  Serial.print("\tD:"); Serial.println(acc_kd);
  Serial.println("**** End PID Values ****");  
}

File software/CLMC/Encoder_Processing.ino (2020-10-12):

/**
 * File: Encoder_Processing.ino
 * Author: Lukas Severinghaus
 * Date: October 11, 2020
 * Purpose: Handles processing of quadrature encoder data.
 * 
 * License:
 * Copyright (C) 2020  Lukas Severinghaus
 * 
 * This program is free software; you can redistribute it and/or
 * modify it under the terms of the GNU General Public License version 3
 * as published by the Free Software Foundation; 
 * 
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
 * You should have received a copy of the GNU General Public License
 * along with this program; if not, write to the Free Software
 * Foundation, Inc., 51 Franklin Street, Fifth Floor, Boston, MA  02110-1301, USA.
 */

/**
 * Encoder notes:
 * Channel A is connected to PCINT0, which is pin 8 on the Arduino Uno
 * Channel B is connected to PCINT1, which is pin 9 on the Arduino Uno
 * 
 * Sources used during development:
 * Interrupt reference: https://thewanderingengineer.com/2014/08/11/arduino-pin-change-interrupts/
 * Bitwise manipulation: https://stackoverflow.com/questions/47981/how-do-you-set-clear-and-toggle-a-single-bit
 * Arduino Ports: https://www.arduino.cc/en/Reference/PortManipulation  
 * Volatile type reference: https://www.arduino.cc/reference/en/language/variables/variable-scope-qualifiers/volatile/
 * Quadrature encoder reference: https://cdn.sparkfun.com/datasheets/Robotics/How to use a quadrature encoder.pdf
 */

#include <avr/interrupt.h>
#define CHANNEL_A 0b00000010 //Pin 8
#define CHANNEL_B 0b00000001 //Pin 9
#define INITIAL_ENC_STATE 0
#define INVALID 2 //Change of count when invalid state detected, likely an encoder jump from slow code.
#define TICKS_PER_ROTATION 1440.0 //Listed as 540.0, but there's three states

//Tick change counter
volatile long encoder_count = 0;

//Lookup table for state changes. 
//See the Sparkfun quadrature reference for more
//information on how this works.
const int8_t encoder_lookup[17] = {0, 1, -1, INVALID,
                                 -1, 0, INVALID, 1,
                                 1, INVALID, 0, -1,
                                 INVALID, -1, 1, 0};

//Initialize the encoder processing                                 
void init_encoders(){
  //Input pullup keeps the pins at a floating state until they are pulled high or low.
  pinMode(8, INPUT_PULLUP);
  pinMode(9, INPUT_PULLUP);

  //Port setting for interrupt setup
  PCICR |= 0b00000001; //Enable port B pin change interrupts
  PCMSK0 |= 0b00000011; //Enable interrupts for PCINT0 and PCINT1
}

//Number of error states encountered
volatile int error_count = 0;
//Stores current and previous encoder states
volatile byte state, p_state = INITIAL_ENC_STATE;


//Captures interrupts from activated pins in Port B.
//Uses a lookup table to get the change in position.
ISR(PCINT0_vect){
  state = PINB & (CHANNEL_A | CHANNEL_B); //Isolate just the two bits from the port input register.
  
  //Calculate the grid position, look it up, and add that value to the current count.
  //See the Sparkfun encoder reference for more info about the grid.
  encoder_count += encoder_lookup[(p_state * 4) + state]; 
  if(encoder_lookup[(p_state * 4) + state] == INVALID){
    error_count++;
  }
  //Save the state for next time.
  p_state = state;
}


//Returns the number of rotations, as a float. 
float get_rotations(){
  return (float) encoder_count / TICKS_PER_ROTATION;
}

//Get the raw encoder tick count.
long get_raw_count(){
  return encoder_count;
}

//Get the number of error conditions encountered.
int get_error_count(){
  return error_count;
}

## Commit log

2020-10-12 Add CAD files
    [Motor Magnet Mount.scad, Motor Magnet Mount.stl]
2020-10-14 Add enclosure files
    [PCB Enclosure V1.SLDPRT, PCB Enclosure V1.STL]
2020-10-15 Add HTML Bill of Materials/Part Placer
2020-10-23 Add motor sensor mount
    [Base Piece V2.stl, Sensor Motor Mount.scad, Upper Piece V1.stl]
2020-11-17 Add several features
    Converted ifdefs to ifs to allow for real time mode switching.
    Added EEPROM config load/save.
    Added help menu.
    Added options for real time tuning.
